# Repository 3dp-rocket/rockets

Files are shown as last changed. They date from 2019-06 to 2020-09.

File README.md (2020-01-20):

# 3D Printed Rockets
The goal of this project is to collaborate on designs of rockets and rocket components for 3D printing.

The first set of designs were developed in [OpenSCAD](https://www.openscad.org/). Using OpenSCAD requires some basic programming skills and it is helpful to have some knowledge of basic math and trigonometry. That said, it is easier to work with existing designs, make tweaks and assemble them into new rockets without knowing any math.

People are encourged to join and add designs they made with other tools. As we learn more togther we will figure out the best tools to use for different projects and skills. 

We want rocket designs to be safe and sound and to follow standard rocket design rules. So we also encourgae contributors to provide documentation about how parts were stress tested and OpenRocket model/simulation results as well as real field test results.

You will find common parts under the 'parts' folder and the first rocket design in this project under 'Janus'. Feel free to add new designs or new parts you have been devloping. Make sure to add a header to your files with you name to get propper attribution. 

To join this project please create an [issue](https://github.com/3dp-rocket/rockets/issues) and type access request in the description. 

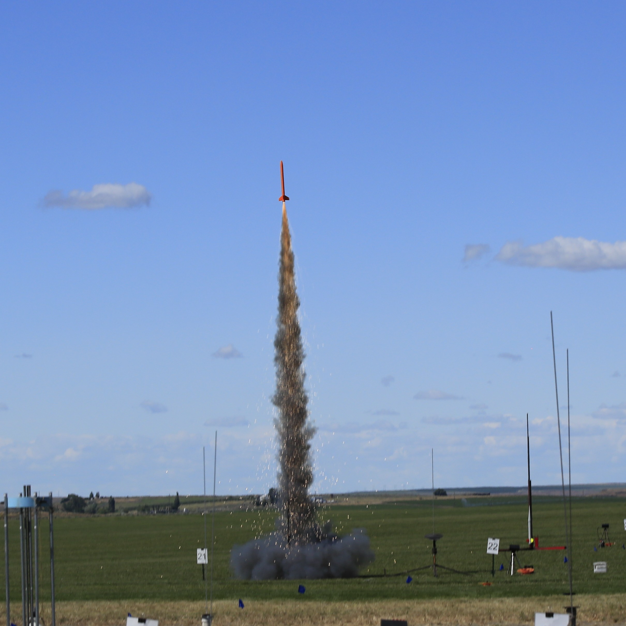
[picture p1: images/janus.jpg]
Tri-cities - Swoosh - 2019 - Richard V.


Janus - HM115 DM - Tri-Cities - Swoosh - 2019

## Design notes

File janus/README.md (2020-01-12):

# Janus

This rocket has been designed so parts can be replaced and assembled without the use of glue (except for the main tube that requires snapping togetther shorter tubes glued with cyanoacrylate). A [blue tube](https://www.alwaysreadyrocketry.com/) is recommended to insulate the motor from the rocket motor support tube.If you use other tubes, you will need to adjust the paper_tube_wall_thickness setting accordingly.

The OpenSCAD [BOSL](https://www.openscad.org/libraries.html) library is required for threads.

[OpenRocket Model](./OpenRocket-29mm.pdf)

Other parts:
* [Kevlar shock cord](https://the-rocketman.com/kevlar-nylon-shock-cords/) or similar.
* [Kevlar cord](https://www.amazon.com/gp/product/B00OVI9XE6/) to attach shock cord to frame.
* [Blue tube (used as motor tube liner for heat insulation)](https://www.alwaysreadyrocketry.com/) or similar.
* [Parachute](https://topflightrecoveryllc.homestead.com/page1.html) - Use a [calculator](https://www.rocketreviews.com/parachute-size-calculator.html) to determine proper size.

Tested with engines:

* 29mm version:
  * Aeroetch G-80
  * Aerotech H-182R-14A and H-115  (9 seconds delay)
  
* [38mm version](./stl/38mm/):
  * Aerotech DMS I500 (12 second delay) - Altitude 4950 ft.

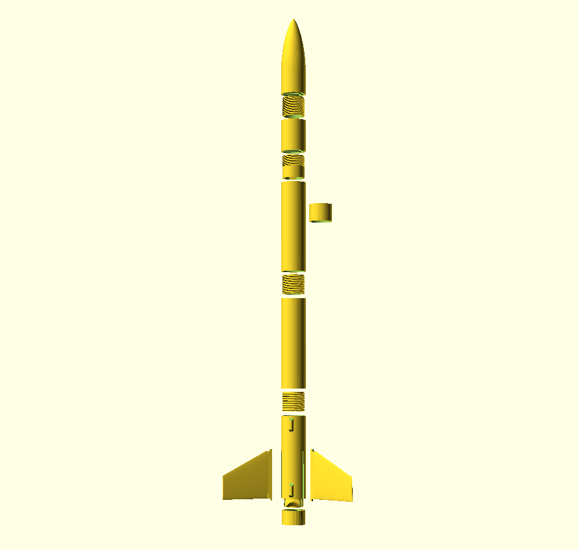
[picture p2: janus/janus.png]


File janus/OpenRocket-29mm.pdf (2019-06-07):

## Rocket Design

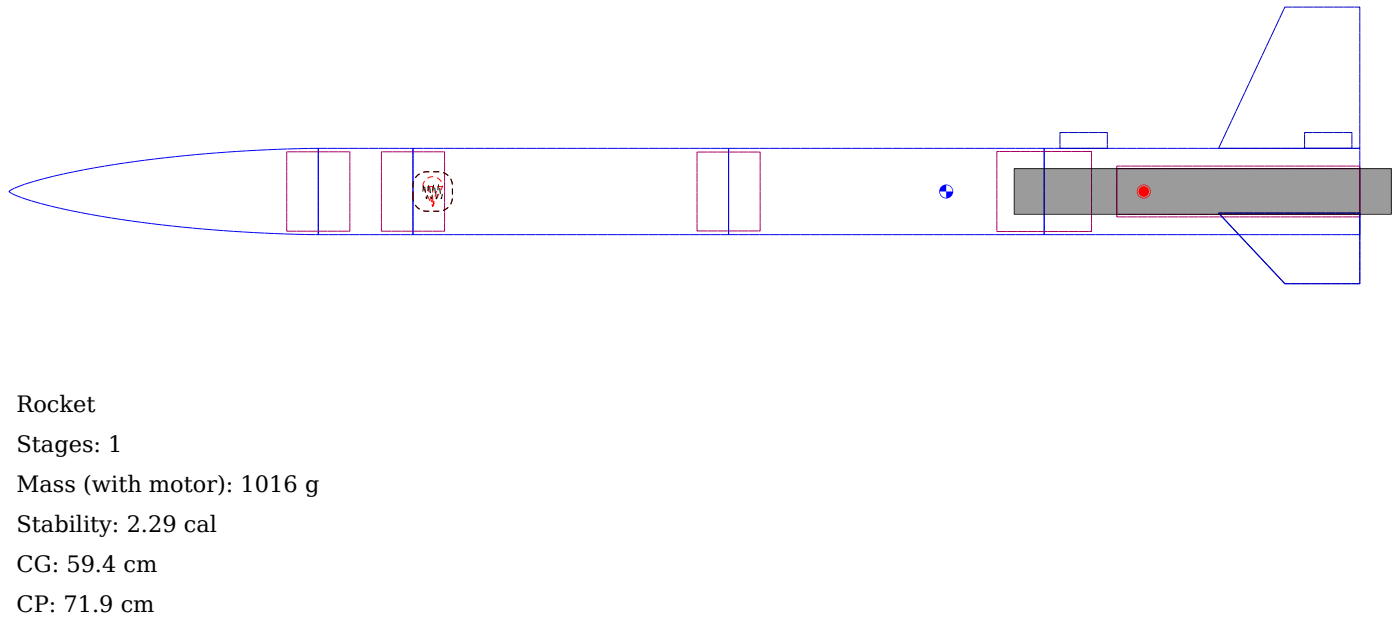
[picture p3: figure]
Rocket; Stages: 1; Mass (with motor): 1016 g; Stability: 2.29 cal

G40W-7

G80-7

Altitude | 360 m
Flight Time | 43 s

Time to Apogee 8.75 s

Optimum Delay 6.5 s

Velocity off Pad 11.9 m/s

Max Velocity | 84.6 m/s
Velocity at Deployment | 6.27 m/s

Landing Velocity 10.7 m/s

Motor | Avg Thrust | Burn Time | Max Thrust | Total Impulse | Thrust to Wt | Propellant Wt | Size
G40W | 46.3 N | 2.13 s | 74.3 N | 99 Ns | 5.40:1 | 53.8 g | 29/124 mm
Altitude | 519 m
Flight Time | 58.7 s

Time to Apogee 9.59 s

Optimum Delay 7.97 s

Velocity off Pad 14.7 m/s

Max Velocity | 123 m/s
Velocity at Deployment | 9.81 m/s

Landing Velocity 10.7 m/s

Motor | Avg Thrust | Burn Time | Max Thrust | Total Impulse | Thrust to Wt | Propellant Wt | Size
G80 | 77.9 N | 1.71 s | 99.4 N | 133 Ns | 9.02:1 | 62.5 g | 29/128 mm

F15-4

F62T-9

H180W-10

Altitude | 74 m
Flight Time | 13.1 s

Time to Apogee 5.79 s

Optimum Delay 2.4 s

Velocity off Pad 5.55 m/s

Max Velocity | 26.3 m/s
Velocity at Deployment | 19 m/s

Landing Velocity 10.5 m/s

Motor | Avg Thrust | Burn Time | Max Thrust | Total Impulse | Thrust to Wt | Propellant Wt | Size
F15 | 14.5 N | 3.42 s | 25.3 N | 49.6 Ns | 1.73:1 | 60 g | 29/114 mm
Altitude | 162 m
Flight Time | 19.5 s

Time to Apogee 6.02 s

Optimum Delay 5.05 s

Velocity off Pad 11.7 m/s

Max Velocity | 56.3 m/s
Velocity at Deployment | 24.6 m/s

Landing Velocity 10.8 m/s

Motor | Avg Thrust | Burn Time | Max Thrust | Total Impulse | Thrust to Wt | Propellant Wt | Size
F62T | 58 N | 0.993 s | 67.6 N | 57.6 Ns | 6.87:1 | 25 g | 29/99 mm
Altitude | 770 m
Flight Time | 80.1 s

Time to Apogee 11.1 s

Optimum Delay 9.8 s

Velocity off Pad 22 m/s

Max Velocity | 182 m/s
Velocity at Deployment | 3 m/s

Landing Velocity 11.2 m/s

Motor | Avg Thrust | Burn Time | Max Thrust | Total Impulse | Thrust to Wt | Propellant Wt | Size
H180W 163 N | 1.3 s | 306 N | 212 Ns | 16.36:1 | 123 g | 29/239
mm

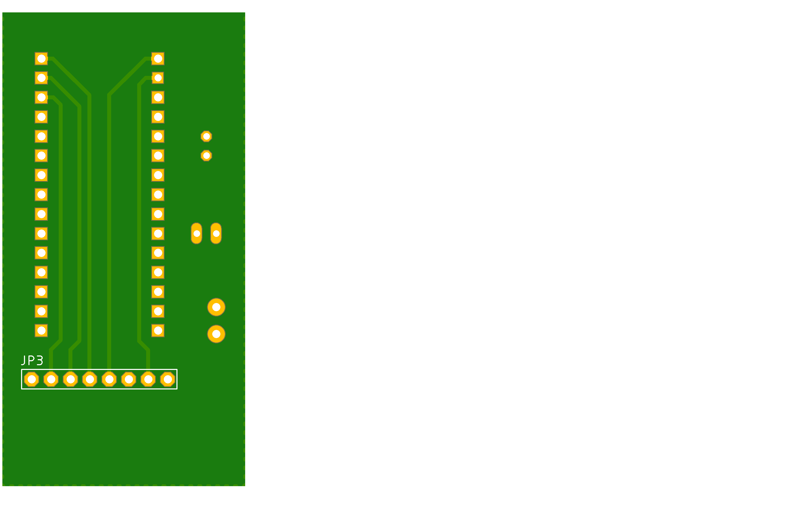
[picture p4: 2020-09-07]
arduino_sense/eagle/logger2/logger2.png

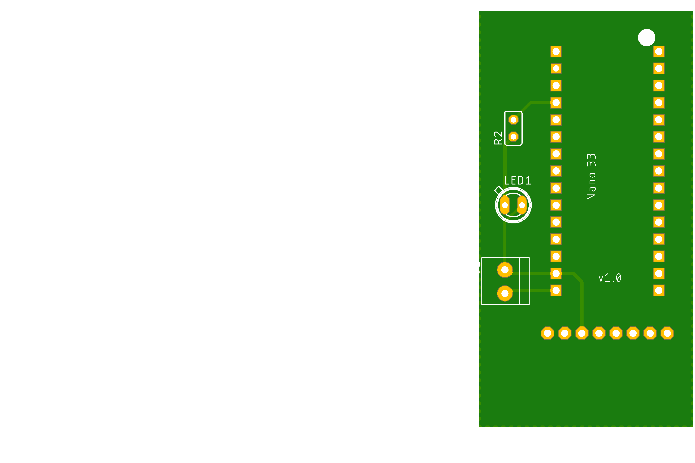
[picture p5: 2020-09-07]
arduino_sense/eagle/logger2/logger2_top.png

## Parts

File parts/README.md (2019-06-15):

# Images - see also [STL](./stl)

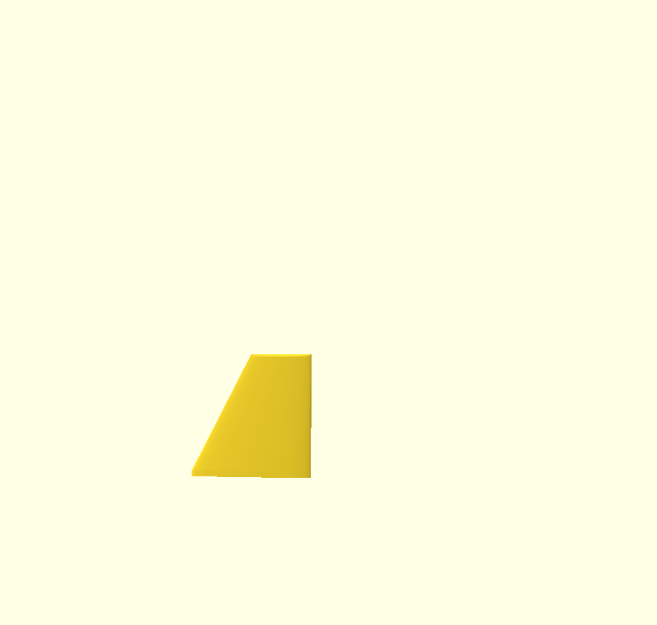
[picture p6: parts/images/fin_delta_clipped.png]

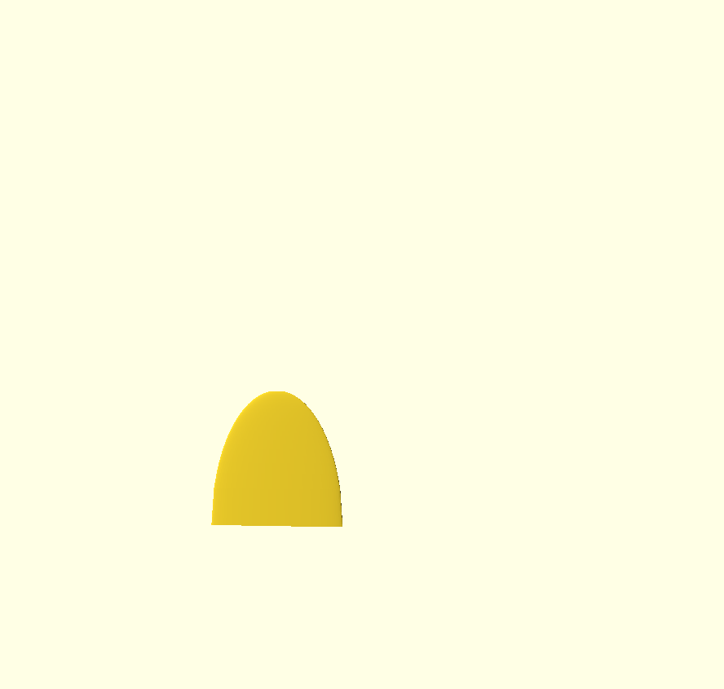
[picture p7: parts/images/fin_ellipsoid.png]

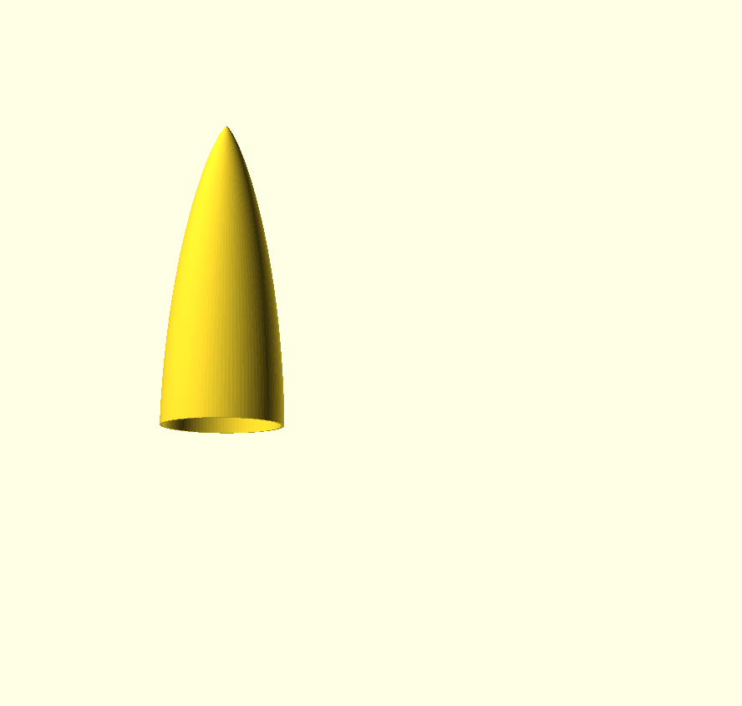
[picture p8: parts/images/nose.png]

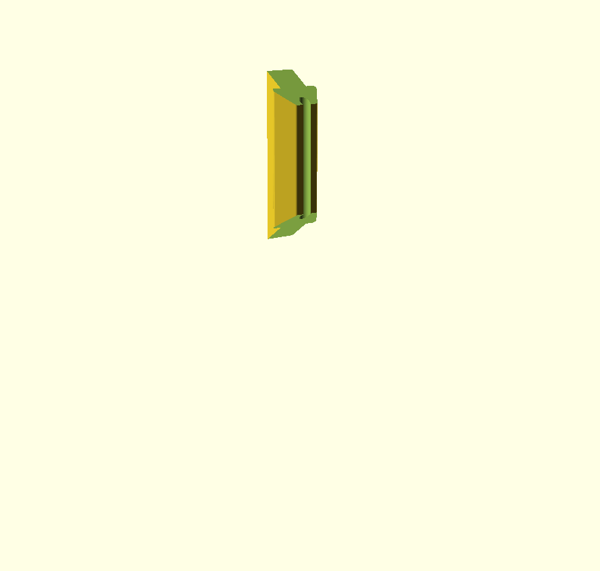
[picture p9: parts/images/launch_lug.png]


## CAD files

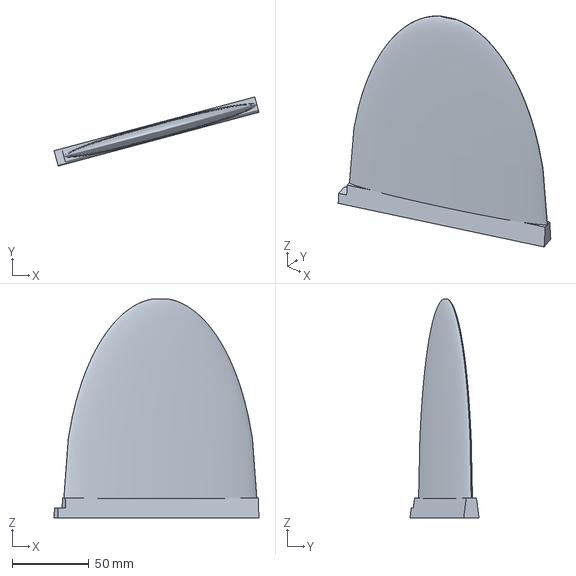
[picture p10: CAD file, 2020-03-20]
janus/3mf/fin.3mf
133.6 x 45.1 x 142.8 mm

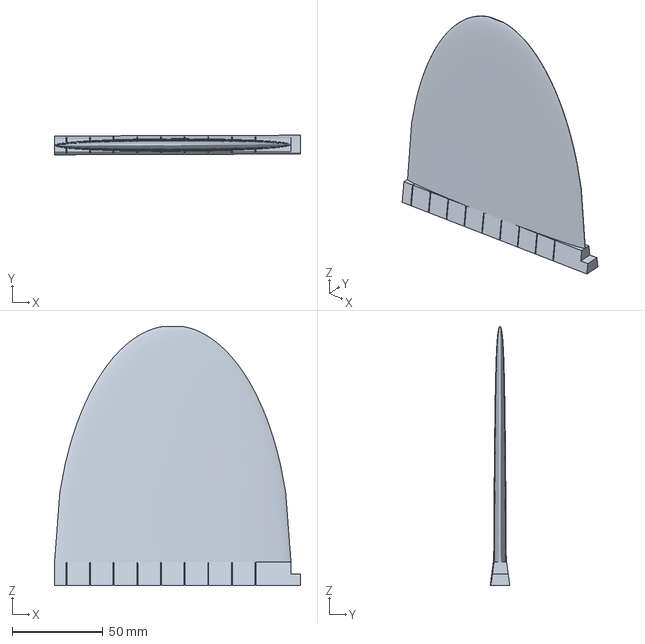
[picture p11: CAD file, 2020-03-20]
janus/3mf/fin_ex.3mf
135.6 x 10.8 x 142.8 mm

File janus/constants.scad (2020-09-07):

TOP_END_THREADED = 0;
TOP_END_SHOULDER = 1;

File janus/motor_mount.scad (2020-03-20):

/*
MIT License

Copyright (c) 2019 Jose D. Saura

Permission is hereby granted, free of charge, to any person obtaining a copy
of this software and associated documentation files (the "Software"), to deal
in the Software without restriction, including without limitation the rights
to use, copy, modify, merge, publish, distribute, sublicense, and/or sell
copies of the Software, and to permit persons to whom the Software is
furnished to do so, subject to the following conditions:

The above copyright notice and this permission notice shall be included in all
copies or substantial portions of the Software.

THE SOFTWARE IS PROVIDED "AS IS", WITHOUT WARRANTY OF ANY KIND, EXPRESS OR
IMPLIED, INCLUDING BUT NOT LIMITED TO THE WARRANTIES OF MERCHANTABILITY,
FITNESS FOR A PARTICULAR PURPOSE AND NONINFRINGEMENT. IN NO EVENT SHALL THE
AUTHORS OR COPYRIGHT HOLDERS BE LIABLE FOR ANY CLAIM, DAMAGES OR OTHER
LIABILITY, WHETHER IN AN ACTION OF CONTRACT, TORT OR OTHERWISE, ARISING FROM,
OUT OF OR IN CONNECTION WITH THE SOFTWARE OR THE USE OR OTHER DEALINGS IN THE
SOFTWARE.
*/


use <BOSL/threading.scad>
use <autofn.scad>
use <hcylinder.scad>
use <couplers.scad>
use <launch_lug.scad>

use <janus_fin.scad>

LUG_ROD_1_8 = 1;
LUG_ROD_3_16 = 2;
LUG_RAIL_8010 =3;

module fin_motor_mount(rocket_od, rocket_id, motor_tube_od, motor_tube_id, motor_height, motor_tube_height, fin_height, fin_slot_width, fin_slot_height, number_of_fins, retainer_height,coupler_height, launch_lug_type, add_thrust_stopper=false)
{
    motor_support_thickness = 0.1 * motor_tube_id;
    motor_tube_od = (motor_tube_id + motor_support_thickness) ;

    // rocket outer shell
    w1 = rocket_od/2.;
    
    difference() {
        union() {
            translate([0,0,retainer_height])
                // outer shell
                hcylinder(motor_tube_height-retainer_height, w1, rocket_id/2.0);
            
            // motor mount
            motor_mount(motor_tube_od, motor_tube_id, rocket_id, motor_height,  fin_height, fin_slot_width, number_of_fins, retainer_height, add_thrust_stopper, motor_tube_height);
        }
        
        fin_slots(motor_tube_od, fin_height,fin_slot_width, motor_tube_height, retainer_height, fin_slot_height, number_of_fins);

    }
    
    // threaded coupler top
    //coupler_height = rocket_id/4.0;
    color("purple", 0.75)
    translate([0,0,motor_tube_height-1])
    rotate([0,180,0])
    female_coupler(rocket_id, coupler_height);  // ?-1
    
    // launch lugs
    if (launch_lug_type>0)
    {
        if (launch_lug_type <3) 
        {
            lug_id = launch_lug_type == LUG_ROD_1_8 ? 4 : 5.75;
            lug_od = 1.3 * lug_id;
            block_width = 0.05 * rocket_id;
            lug_length = max(rocket_od/1.5, 16); //body_id/2;
            rocket_wall_width = rocket_od-rocket_id;
            lug_rotation = 60+(number_of_fins==3?15:0);

            rotate([0,0,lug_rotation])
            {
                lug_x = (rocket_id)/2 + lug_od/2 + rocket_wall_width -0.01;//+ block_width/2;
                translate([lug_x,0,retainer_height + lug_length/2 ])
                {
                    lug(lug_od, lug_id, lug_length, block_width);
                }
            
                translate([lug_x,0,motor_tube_height-lug_length])
                {
                    lug(lug_od, lug_id, lug_length, block_width);
                }

            }
        }
        else
        {
            lug_rotation = 60+(number_of_fins==3?15:0);
            lug_heigth = 0.75 * rocket_id;
            rotate(lug_rotation)
            translate([rocket_id/2+6,0,retainer_height])
            rotate(-90)
            rail_launch_lug(lug_heigth);
            
            translate([0,0, motor_tube_height - lug_heigth ])
            {
                rotate(lug_rotation)
                translate([rocket_id/2+6,0,0])
                rotate(-90)
                rail_launch_lug(lug_heigth);
            }
        }

    }
    
    
}

module motor_mount(motor_tube_od, motor_tube_id, rocket_id, motor_height, fin_height, fin_slot_width, number_of_fins, retainer_height, add_thrust_stopper, motor_tube_height)
{
    // motor mount
   top_ring_heigth = motor_height * 0.15;
   z = motor_height + retainer_height - top_ring_heigth/2;
   max_z = motor_tube_height - rocket_id/2; // below female coupler thread
   top_ring_z = min(z, max_z);
    
    difference() {
        union()
        {
            w2 = motor_tube_id / 2.0 ; //+ 0.15;
            translate([0,0,retainer_height])
                color("yellow", 0.6)
                // the motor tube (proper)
                hcylinder(motor_tube_height-retainer_height, motor_tube_od/2., w2);
            
            if (add_thrust_stopper)
                color("blue")
                translate([0,0,motor_height])
                    hcylinder(10, w2, 0.7*w2);
            
            // thread for motor retainer
            thread_od = (rocket_id+motor_tube_od)/2.;
            pitch = 2.0;
            starts=1;
            color("blue")
            difference() {
                // Retainer male thread 
                trapezoidal_threaded_rod(
                d=thread_od-0.2, 
                l=retainer_height, 
                internal=false,
                thread_angle=30,
                thread_depth=pitch/2,
                pitch=pitch, 
                left_handed=false, 
                bevel=true, 
                starts=starts,
                align= [0,0,1], 
                $fa=1, $fs=1);

                translate([0,0,-.1])
                    cylinder(retainer_height+10, motor_tube_id / 2.0, motor_tube_id / 2.0, $fn=fn(motor_tube_id));
            }
                
            color("green", 0.8)
            {
                // supports along the tube where fins will go
                // they connect the motor tube to outer shell and support the fins
                // supports start above the retainer ring (retainer_height)
                for(a=[0:360/number_of_fins:360]) {
                    rotate([0,0,a-2.5])
                    {
                        translate([0,0,retainer_height])
                        {
                            t = (rocket_id-motor_tube_od)/2. * 1.1;
                            rotate_extrude(angle=35) //, convexity=10)
                            translate([motor_tube_od/2.-0.5, 0, 0])  // manifold error =>
                            square([t,motor_height], center=false); //manifold error+.2
                        }
                    }
                }
                
                // three rings at differnt heights to support/connect 
                // the motor tube to the outer shell
                translate([0, 0, retainer_height])
                    hcylinder(5, rocket_id/2.0, motor_tube_od/2.0);
                translate([0, 0, (motor_height+retainer_height)/2.])
                    hcylinder(5, rocket_id/2.0, motor_tube_od/2.0);
                translate([0, 0, top_ring_z])
                    hcylinder(top_ring_heigth, rocket_id/2.0, motor_tube_od/2.0);
                
                
            }
            
        }

     }
   
}

module fin_slots(motor_tube_od, fin_height, fin_slot_width, motor_tube_height, retainer_height, fin_slot_height, number_of_fins)
{
    // slots
    for(a=[0:360/number_of_fins:360]) {
        rotate([0,0,a])
        {
           translate([0,0,0])
           {
                rotate([0,0,15])
                translate([motor_tube_od/2-0*fin_slot_height/4, 0, 0]) {
                   rotate([0,0,-90]) {
                    key_h = .04 * fin_height;
                    h =fin_height + retainer_height + key_h;
                       difference() {
                           /* linear_extrude(h)
                                polygon(polygon_slot(fin_slot_height, fin_slot_width));
                           */
                           fin_support(h, fin_slot_height, fin_slot_width);
                           // remove tiny top section of slot to make room for the  "key"
                           // under the body shell. 
                           translate([0, fin_slot_height/1.0, h-key_h/2.])
                            cube([fin_slot_width,fin_slot_height/2,key_h], center=true);
                       }
                       
                   }
                    
                }

            }
        }
    }
    
}

function polygon_slot(fin_slot_height,fin_slot_width) = 
[[-fin_slot_width/2.,0],[-fin_slot_width/3.,fin_slot_height],[fin_slot_width/3.,fin_slot_height],[fin_slot_width/2.,0] ];

// 101.14, 91.9455, 64.5231, 58.6574, 135, 200, 
//  132.806, 14.6644, 18.3084, 35.1944, 3

//rocket_od, rocket_id, motor_tube_od, motor_tube_id, motor_height, motor_tube_height, fin_height
//fin_slot_width, fin_slot_height, retainer_height,launch_lug_type, add_thrust_stopper=false)
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

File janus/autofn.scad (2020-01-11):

function fn(d) = max(50, round(d) * ($preview?1:3)); 
function steps(d) = max(80,4*round(d)); //# used for threading - odd numbers will cause error: PolySet has nonplanar faces. 


//echo("$fn(50)", fn(50));

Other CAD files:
janus/sleeve.stl
janus/stl/29mm/piston.stl
janus/stl/38mm/coupler2_baffle.stl
parts/stl/fin_ellipsoid.stl
janus/ejection_charge_holder38.stl
janus/stl/38mm/piston.stl
parts/stl/altimeter_holder.stl
janus/ejection_charge_holder.stl
janus/stl/29mm/escapement_ring.stl
janus/stl/38mm/coupler1.stl
parts/stl/fin_delta_clipped.stl
janus/stl/29mm/parachute_extension.stl
janus/stl/38mm/coupler4.stl
parts/stl/baffle.stl
janus/stl/29mm/parachute_middle_extension.stl
janus/stl/38mm/retainer.stl
janus/cord_attachment.scad
janus/Naca_sweep.scad
janus/Threading.scad
janus/couplers.scad
janus/extension_tube.scad
janus/hcylinder.scad
janus/instrument_compartment.scad
janus/janus.scad
janus/janus_fin.scad
janus/janus_nose.scad
janus/launch_lug.scad
janus/parachute_compartment.scad
janus/piston.scad
janus/retainer.scad
janus/stl/29mm/coupler1.stl
janus/stl/29mm/coupler2.stl
janus/stl/29mm/coupler3.stl
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

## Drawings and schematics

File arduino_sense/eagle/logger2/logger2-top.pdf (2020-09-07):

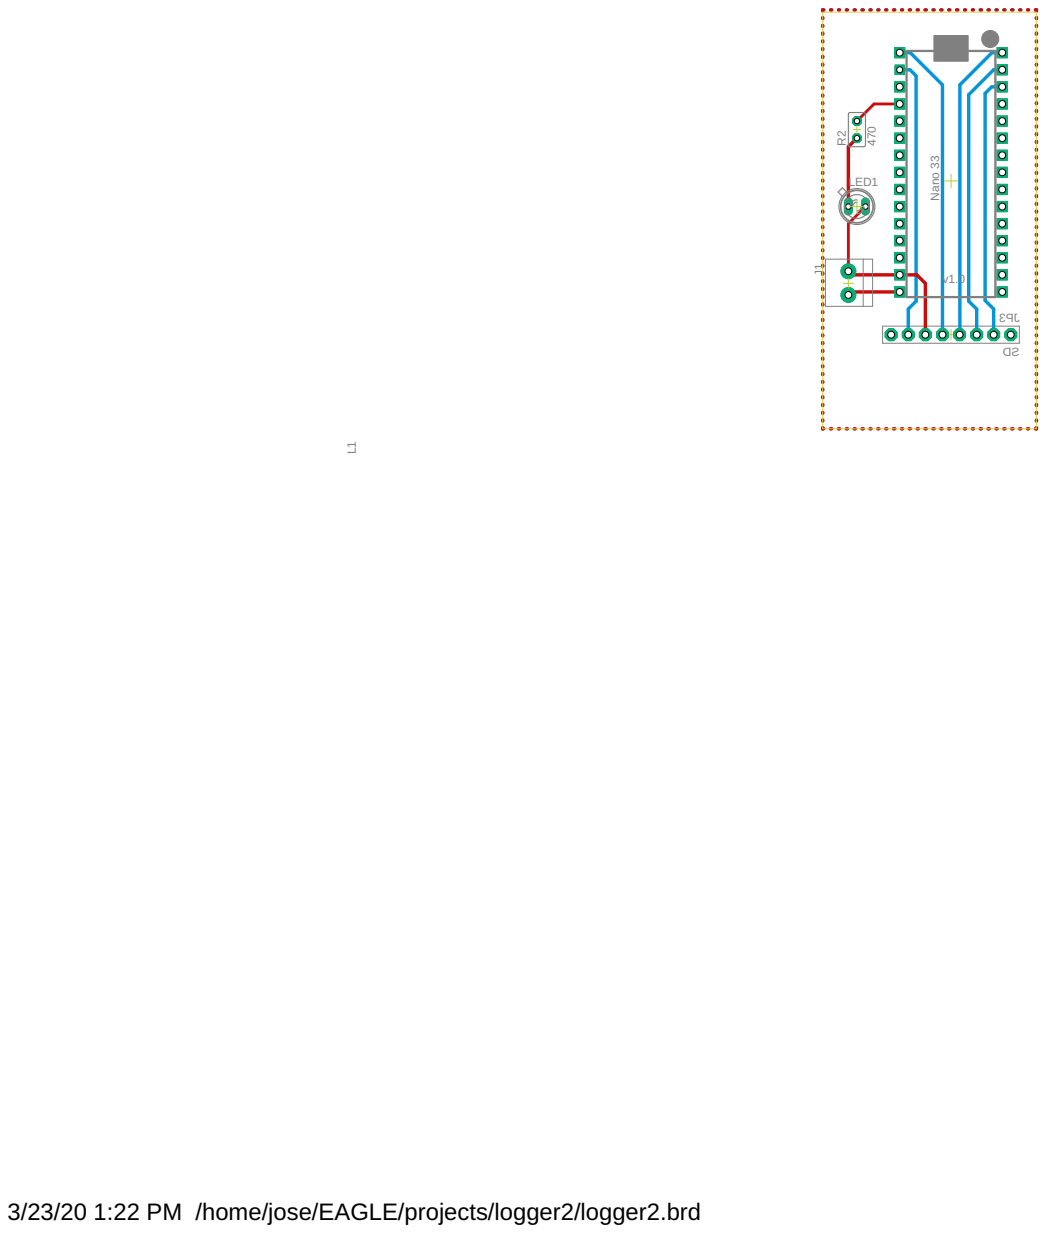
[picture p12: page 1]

3/23/20 1:22 PM /home/jose/EAGLE/projects/logger2/logger2.brd

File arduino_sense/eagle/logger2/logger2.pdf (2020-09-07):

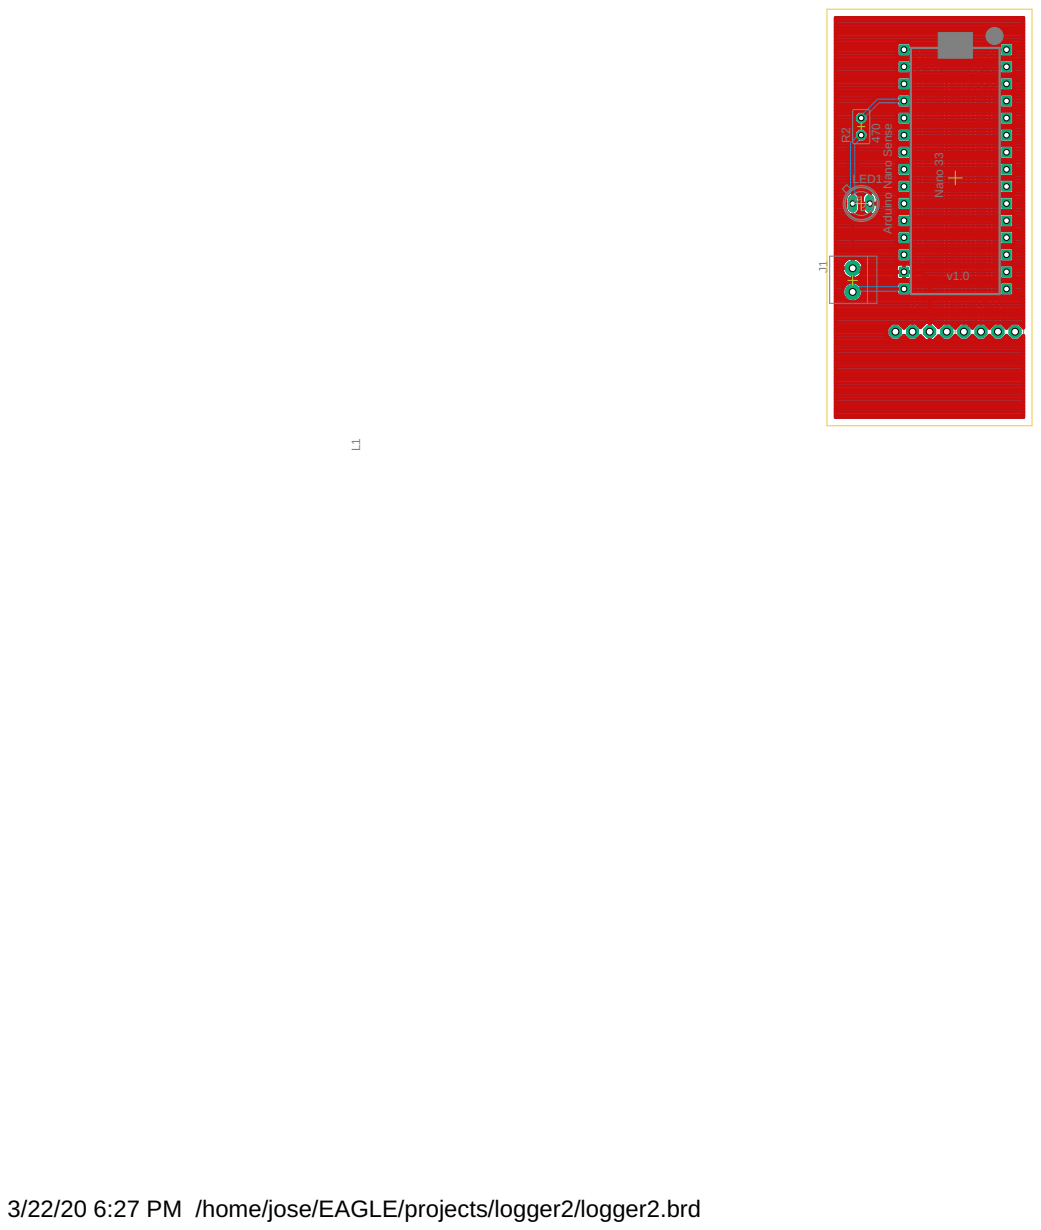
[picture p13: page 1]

3/22/20 6:27 PM /home/jose/EAGLE/projects/logger2/logger2.brd

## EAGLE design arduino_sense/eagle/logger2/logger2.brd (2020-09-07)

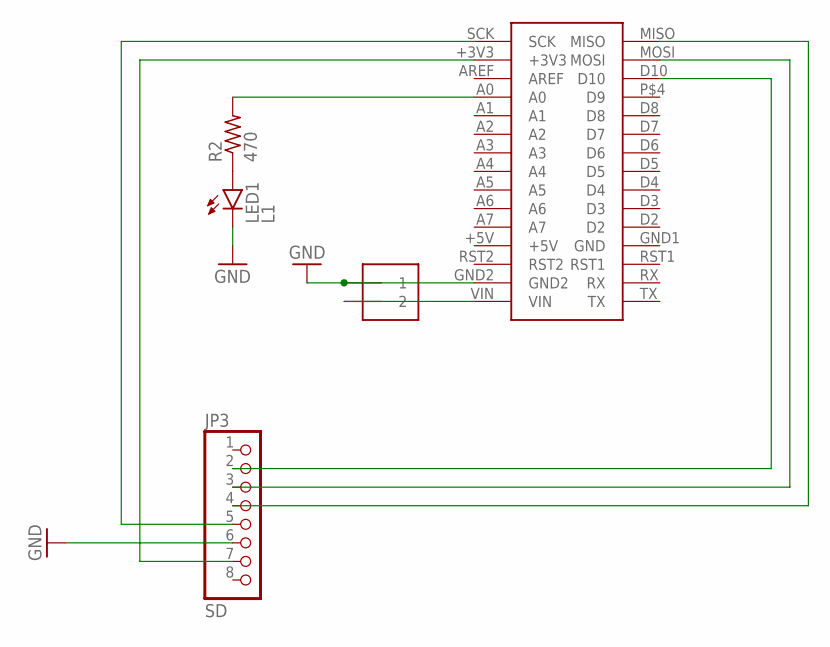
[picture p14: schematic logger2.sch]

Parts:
J1: 1X2-3.5MM
JP3: SD; 1X08-BIG
LED1: L1; SFH482
MC1: NANODEVICE; NANO
R2: 470; V526-0

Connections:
GND: J1.1, JP3.6, LED1.K (C), MC1.GND2
unnamed: JP3.5, MC1.SCK
unnamed: JP3.7, MC1.+3V3
unnamed: J1.2, MC1.VIN
unnamed: JP3.3, MC1.MOSI
unnamed: JP3.4, MC1.MISO
unnamed: LED1.A, R2.1
unnamed: JP3.2, MC1.D10
unnamed: MC1.A0, R2.2

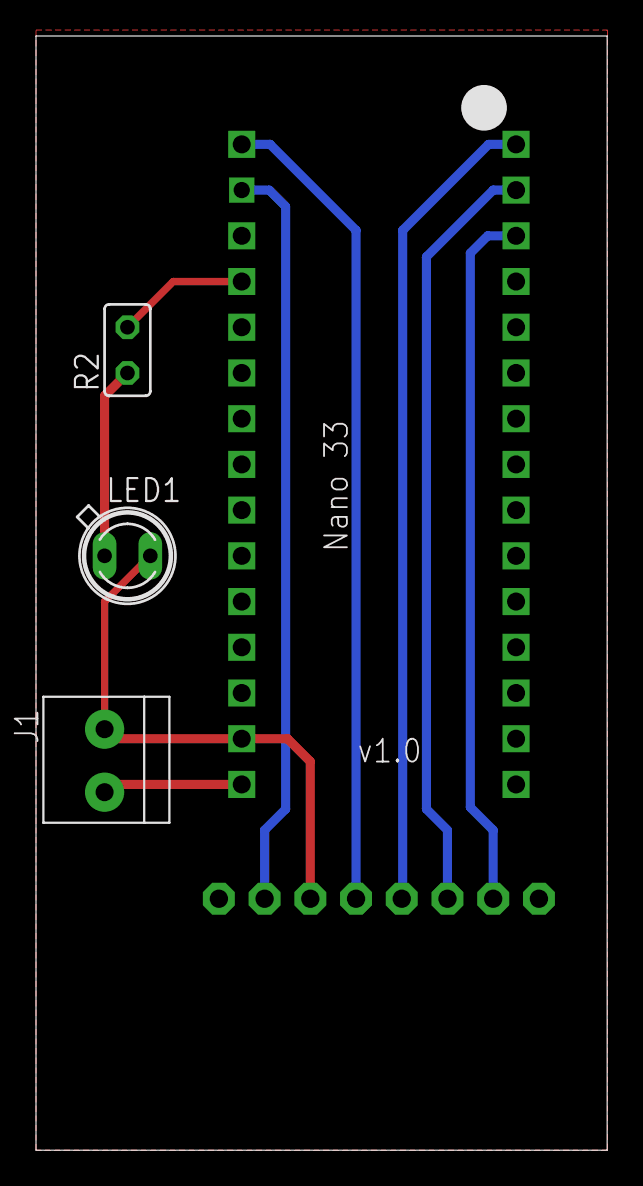
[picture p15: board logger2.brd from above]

Board: 2 copper layers, 31.7 x 61.9 mm, 5 parts (1 on the bottom side), 9 nets.

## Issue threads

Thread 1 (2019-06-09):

Request access

tggmbi, 2019-06-09:

Beeblebrox666, 2020-01-08:
I am interested in joining this discussion, when available, I would like to post my 3d printed stuff and flight information.

zwitterion, 2020-01-10:
Hi Beeblebrox666,

I sent you an invite from github so you can join the project. Let me know if you run into any issues. If you prefer you can also email me directly at: josesaura@hotmail.com

Looking forward to seeing your designs,

Jose

________________________________
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

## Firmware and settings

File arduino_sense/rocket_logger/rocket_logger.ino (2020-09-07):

// https://www.arduino.cc/en/Guide/NANO33BLESense
/*
 *  The circuit:
   SD card attached to SPI bus as follows:
 ** MOSI - pin 11
 ** MISO - pin 12
 ** CLK - pin 13
 ** CS - pin 10 
 * 
 * Attach optional led with resistor to pin status_led (8)

 */
#include <Arduino_LPS22HB.h>
#include <Arduino_LSM9DS1.h>   
#include <Arduino_APDS9960.h>  // color, gestures
#include <Arduino_HTS221.h>

#include <SPI.h>
#include <SD.h>

// buffer size for data we will write to the SDcard
#define BUFFER_SIZE 2048

// file name to use for writing
String filename;

const int chipSelect = 10;
byte status_led = A0;

File dataFile;

// string to buffer output
String buffer;

enum States {
  warmup,
  waiting_for_event,
  recording,
  done
};

States state;

struct SensorData {
  float pressure=0;
  float ax, ay, az = 0; // accelerometer
  bool accel_error;
  
  float gx, gy, gz = 0; // gyro
  bool gyro_error;
  
  float mx, my, mz = 0;  // magnetometer
  bool magnetometer_error;

  int r,g,b = 0;  // color

  float temperature=0;
  float humidity=0;

  
} signals, previous_signals;


uint16_t count_files(File dir) {

  uint16_t count = 0;

  while (true) {

    File entry =  dir.openNextFile();
    if (! entry) {
      // no more files
      break;
    }
    count++;
  }
  
  return count;
}



void setup() {
  
  // Open serial communications and wait for port to open:
  Serial.begin(9600);
  delay(1000);
  //while (!Serial) {
  //  ; // wait for serial port to connect. Needed for native USB port only
  //}

  if (!BARO.begin()) {
    Serial.println("Failed to initialize pressure sensor!");
  }
  if (!IMU.begin()) {
    Serial.println("Failed to initialize IMU!");
  }

  if (!APDS.begin()) {
    Serial.println("Error initializing APDS9960 (color, gesture) sensor!");
  }

  if (!HTS.begin()) {
    Serial.println("Failed to initialize humidity temperature sensor!");
  }
  
  Serial.println("Initializing SD card...");

  // see if the card is present and can be initialized:
  if (!SD.begin(chipSelect)) {
    Serial.println("Card failed, or not present");
    // don't do anything more:
    while (1);
  }

  // generate new file name
  Serial.println("Generating new file name");
  File root = SD.open("/");
  uint16_t count = count_files(root);
  filename = String("data")+String(count) + ".csv";
  root.close();
  Serial.print("file name:");
  Serial.println(filename);
  
  // open the file. note that only one file can be open at a time,
  // so you have to close this one before opening another.
  dataFile = SD.open(filename, FILE_WRITE);
  if (!dataFile) {
    Serial.print("error opening ");
    Serial.println(filename);
    while (1);
  }

  Serial.println("SD card initialized.");

  // reserve 2kB for String used as a buffer
  buffer.reserve(BUFFER_SIZE);

  // set LED pin to output, used to blink when writing
  pinMode(status_led, OUTPUT);
  digitalWrite(status_led, LOW);

  state = warmup;

}

// time since last update in micros
unsigned long next_update = 0;
uint16_t num_samples = 0;
uint16_t loop_count  = 0;

void read_sensors()
{

  signals.pressure = BARO.readPressure(KILOPASCAL);  // PSI, MILLIBAR, KILOPASCAL
  
  if (IMU.accelerationAvailable()) {
        IMU.readAcceleration(signals.ax, signals.ay, signals.az);
        signals.accel_error = false;
  }
  else signals.accel_error = true;

  if (IMU.gyroscopeAvailable()) {
        IMU.readGyroscope(signals.gx, signals.gy, signals.gz);
        signals.gyro_error = false;
  } else signals.gyro_error = true;

  if (IMU.magneticFieldAvailable()) {
        IMU.readMagneticField(signals.mx, signals.my, signals.mz);
        signals.magnetometer_error = false;
  } else signals.magnetometer_error = true;


  if (APDS.colorAvailable()) {
    APDS.readColor(signals.r, signals.g, signals.b);
  }

  signals.temperature = HTS.readTemperature();
  signals.humidity = HTS.readHumidity();
  
}

#define PRESSURE_THRESHOLD 0.2
#define ACCEL_THRESHOLD 1.1
#define GYRO_THRESHOLD 20

bool trigger() {

    
    if (abs(previous_signals.pressure - signals.pressure)> PRESSURE_THRESHOLD)  {  // aprox: 15 meters change
      Serial.println("pressure:");
      Serial.print(previous_signals.pressure);
      Serial.print(" ");
      Serial.println(signals.pressure);
      return true;
    }
     
    if ((abs(previous_signals.ax - signals.ax)>ACCEL_THRESHOLD) || (abs(previous_signals.ay - signals.ay)>ACCEL_THRESHOLD) || (abs(previous_signals.az - signals.az)>ACCEL_THRESHOLD)) {
      Serial.println("Accel");
      Serial.println(previous_signals.ax);
      Serial.print(" ");
      Serial.println(signals.ax);

      Serial.print(previous_signals.ay);
      Serial.print(" ");
      Serial.println(signals.ay);

      Serial.print(previous_signals.az);
      Serial.print(" ");
      Serial.println(signals.az);
      return true;
    }


    if ((abs(previous_signals.gx - signals.gx)>GYRO_THRESHOLD) || (abs(previous_signals.gy - signals.gy)>GYRO_THRESHOLD) || (abs(previous_signals.gz - signals.gz)>GYRO_THRESHOLD)) {
      Serial.println("Gyro");
      Serial.println(previous_signals.gx);
      Serial.print(" ");
      Serial.println(signals.gx);

      Serial.print(previous_signals.gy);
      Serial.print(" ");
      Serial.println(signals.gy);

      Serial.print(previous_signals.gz);
      Serial.print(" ");
      Serial.println(signals.gz);
      return true;
    }

  return false;
  
}

void write_header()
{
  char header[] = "time\tpressure\tax\tay\taz\tgyro_x\tgyro_y\tgyro_z\tmx\tmy\tmz\tr\tg\tb\ttemperature\thumidity";
  dataFile.println(header);

}
bool record_signals()
{
    if (buffer.length()>BUFFER_SIZE)
    {
      // does this work?
      Serial.println("Buffer is full");
      return false;
    }
    
    // Append data to buffer
    buffer += String(micros());
    buffer += String('\t');
    buffer += String(signals.pressure);
    buffer += String('\t');
  
    buffer += String(signals.ax);
    buffer += String('\t');
    buffer += String(signals.ay);
    buffer += String('\t');
    buffer += String(signals.az);
    buffer += String('\t');
  
    buffer += String(signals.gx);
    buffer += String('\t');
    buffer += String(signals.gy);
    buffer += String('\t');
    buffer += String(signals.gz);
    buffer += String('\t'); 
    
    buffer += String(signals.mx);
    buffer += String('\t');
    buffer += String(signals.my);
    buffer += String('\t');
    buffer += String(signals.mz);
    buffer += String('\t');

    buffer += String(signals.r);
    buffer += String('\t');
    buffer += String(signals.g);
    buffer += String('\t');
    buffer += String(signals.b);
    buffer += String('\t');
    
    buffer += String(signals.temperature);
    buffer += String('\t');
    buffer += String(signals.humidity);

    

    buffer += "\r\n";
    
    // check if the SD card is available to write data without blocking
    // and if the buffered data is enough for the full chunk size
    unsigned int chunkSize = dataFile.availableForWrite();
    if (chunkSize && buffer.length() >= chunkSize) {
      // write to file and blink LED
      digitalWrite(status_led, HIGH);
      dataFile.write(buffer.c_str(), chunkSize);
      digitalWrite(status_led, LOW);
  
      // remove written data from buffer
      buffer.remove(0, chunkSize);
    }

  return true;
  
}
void loop() {

  read_sensors();

  switch(state) {
    case warmup:

      digitalWrite(status_led, LOW);
      
      if (loop_count>1000) {
        Serial.println("warmed up-waiting for event");
        state = waiting_for_event;
        previous_signals = signals;
        write_header();
      }
      else {
        if (loop_count % 100 == 0) {
          digitalWrite(status_led, HIGH);
          Serial.print("warmup ");  
          Serial.println(loop_count);
        }
      }
            
      delay(10);
      break;

    case waiting_for_event:
      digitalWrite(status_led, HIGH);
      if (trigger()) {
        state=recording;
        next_update = 0;
        digitalWrite(status_led, LOW);
      } 
      else 
        delay(1);
        
      break;
    
    case (recording):
      if (micros() > next_update) {
        record_signals();
        next_update = micros() + 1000;
        num_samples++;

          if (num_samples % 100 == 0) {
            Serial.print("Number of samples: ");
            Serial.println(num_samples);
          }
  
          if (num_samples > 40000){
            dataFile.close();
            state = done;
            Serial.println("collected more than 40000 samples."); 
          }
      }
      else 
        delay(1);
      
      break;
      
    default:
      delay(10);
      break;
  }

  
  loop_count++;

}

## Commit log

2019-05-30 created nose.scad
    [nose.scad]
2019-06-01 added retainer and lugs
    [janus.scad, launch_lug.scad, retainer.scad]
2019-06-13 ellipsoid fin
    [fin.scad]
2019-06-13 thicker fin
    [coupler1.stl, coupler2.stl, coupler3.stl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]
2019-06-13 changed fin cord length
    [janus.scad]
2019-06-15 fixed ring height
    [motor_mount.scad]
2019-09-15 new piston, ejection charge test device
    [Untitled.scad, couplers.scad, janus.scad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]
2019-09-29 updated piston
    [coupler1.stl, coupler2.stl, coupler3.stl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]
2019-12-21 preparing to test rocket with 54mm motor
    [Threading.scad, Untitled.scad, baffle.scad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]
2020-01-11 changed threading library to OpenSCAD std library
    [autofn.scad, couplers.scad, extension_tube.scad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]
2020-01-11 updated stl's
    [coupler1.stl, coupler3.stl, coupler4.stl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]
2020-01-12 changed motor retainer thread size
    [janus.scad]
2020-01-20 fix fin support gap in motor tube
    [couplers.scad, extension_tube.scad, janus.scad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]
2020-01-20 track *.stl files using git lfs
2020-01-20 udpated stls
    [coupler3.stl, escapement_ring.stl, fin.stl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]
2020-01-23 new ejection charge holder for static tests
    [couplers.scad]
2020-01-29 added distance table
    [NFPA-1127-Tables.xlsx]
2020-03-20 added data logger arduino sense sketch
    [altimeter_holder.stl, baffle.stl, coupler1.stl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]
2020-03-20 removed stl due to github limit
    [coupler1.stl, coupler2.stl, coupler2m.stl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]
